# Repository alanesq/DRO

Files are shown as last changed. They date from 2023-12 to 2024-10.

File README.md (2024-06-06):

# DRO - A super cheap Digital Readout (DRO) for lathes, milling machines etc. 

<br>My homemade ESP32 based DRO which conists of:
 - [Cheap Yellow Display](https://github.com/witnessmenow/ESP32-Cheap-Yellow-Display) &ensp; (A.K.A. ESP32-2432S028R) which costs around £12 from Aliexpress
 - Digital calipers which cost under £2.50 each on Aliexpress 
 - Plus a few transistors, general wiring etc... 

As a result, building a three-axis DRO for your milling machine or lathe can set you back less than £25 (around $30). <br><br>

<p align="center" width="100%">
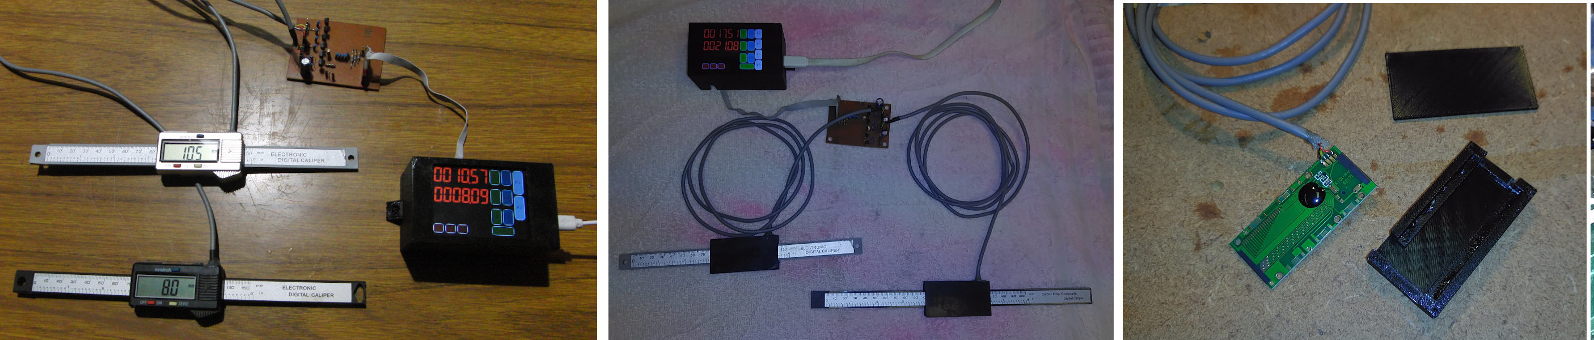
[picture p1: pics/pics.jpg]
  <br><br>
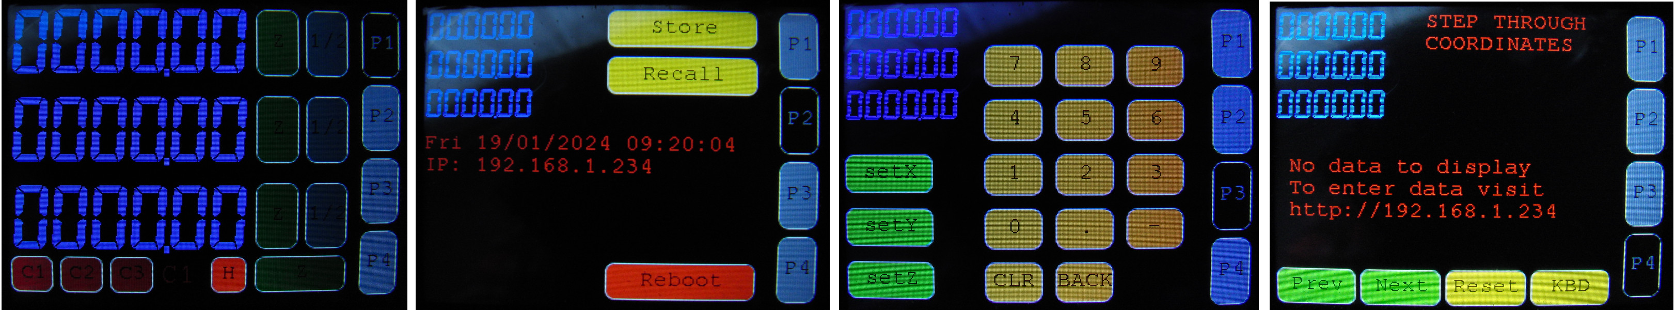
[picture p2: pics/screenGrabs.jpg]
  
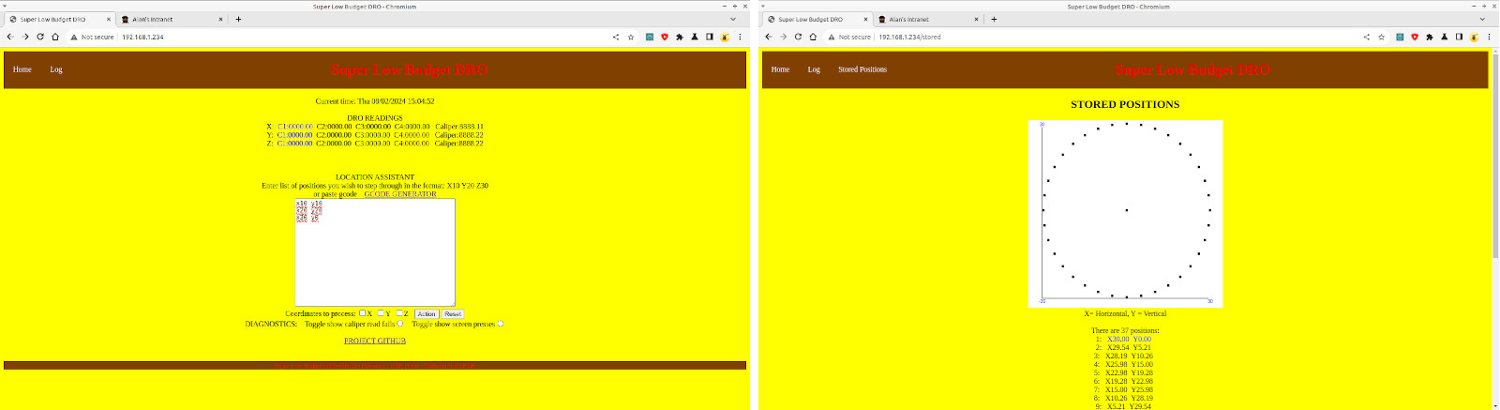
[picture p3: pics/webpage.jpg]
  <br><br>
</p>

I wanted a Digital Readout (DRO) for both my lathe and milling machine. However, the cheapest options available was still going to cost me several hundred pounds, which I just couldn’t justify spending. I also suspected that the cheapest DRO on the market would probably fail after a short time anyway going on my past experience of cheap electronics.  Therefore, I decided to see if I can create my own as inexpensively as possible.  I think it safe to say that I have achieved this goal :-)<br>
Not only did this save me spending a lot of money when I do not even know how much I would use one but it means I can modify it to my exact requirements and it will always be easily fixable.<br><br>

The libraries required for this sketch are detailed [HERE](https://github.com/alanesq/DRO/tree/main/LIBRARIES)<br>
Note that the "TFT_eSPI" library needs to be modified to work with the CYD and if your CYD has two USB ports there is a further change to this required.

## Patterns

Rather than a complicated hole pattern facilities on this DRO (for drilling a circle of holes etc.) I decided it would be easier and more versatile to enter the coordinates of the positions required via the web page, these coordinates can then be steped through from the DRO screen (page 4).  <br>
The coordinates are ented as a simple list in the format:<br>
```
x0 y0
x0 y10
x10 y0
x10 y10
```
It also has the option to paste simple gcode, this gives the ability to create your own bolt hole patterns etc. using whatever software you preffer (A good choice would be Inkscape and [Krabzcam](https://github.com/mkrabset/krabzcam) ) or even easier you can use online tools for creating them &ensp; e.g. [online gcode tools](https://www.intuwiz.com/drilling.html) <br><br>

## Digital calipers

The cheap calipers only have a range of 150mm although longer 200mm or even 300mm are available on eBay for under £20, this is probably enough for my requirements although I have had some longer PCBs created which were designed by "Limi DIY" and they appear to work and extend the range to around 400mm.  There is the possibility to link these together although the join would need to be very accurate.  I had 5 lengths made which came in at £10 each so they are not cheap by the standards of this project but not as expensive as you may think. <br> 
&ensp; &ensp; [extending the range](https://hackaday.com/2021/08/05/custom-caliper-tracks-for-when-youre-going-the-distance/) &ensp; - &ensp;
[PCBway order link](https://www.pcbway.com/project/shareproject/Digital_Caliper_Hack_Mod_new_2021.html) <br>

Especially on my lathe I found that I actually did not need to have a long caliper as the work I require to measure tends to be in a small area so I have just attached a short caliper body to the machine but the slider is attached via a magnet, so if I extend beyond the calipers reach it simply detatches and then re-attaches when it returns.  This works really well and made installing the DRO very simple.  I also have the third caliper on my lathe fully attached with magnets and have two locations I can choose to attach it.  [see pic here](https://github.com/alanesq/DRO/blob/main/pics/lathe1.jpg)<br>

These cheap calipers really are amazing for the price, in fact they are so cheap that it feels like they are almost being given away, also, I find the cheaper ones with a plastic slider are better than metal ones in this application as you do not get issues with the metal contacting the metal of your machine which can cause issues.  Big Clive has made a nice video showing what is inside them and how to take them apart etc.: &ensp; [Big Clive](https://www.youtube.com/watch?v=fKSSY1gzCEs) <br>
I have read that because of interference issues this type caliper is not at all suitable to use as a DRO and I was starting to agree as I had a lot of trouble at first with this but I eventually found the solution (see bottom of page for more info.).<br>
One good thing that I was not expecting is you still get two decimal places from these very cheap calipers even though they only display one on their LCD, as can be seen in the pictures above. <br>

The most recent calipers i have purchased were:   [eBay £5.40 each](https://www.ebay.co.uk/sch/i.html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) , [Aliexpress £10 for 4](https://www.aliexpress.com/item/1005005699974701.html) <br><br>   

## Warnings!

The well known problem with these cheap calipers is the battery goes flat if you do not use them for a while, it turns out that they are producing the data we use here all the time, even when turned off.  I bought one of the longer calipers recently which looks like it is a "new/impoved" design which has got round this issue by turning off the data all together which is very bad news if you want to use it for this project.  So if you are buying calipers I suggest you try to buy the older style ones if you can as the newer ones do not seem to support data, the good news is these will be the cheapest ones.  You can still use the reader from a cheaper caliper on this longer bar if you do have one though.  I understand that some of these calipers use a different data standard although all the ones I have tried are the same.  The calipers would not cope well to getting wet so you will need to cover them well if this is likely to happen.

## Misc info:

I have recently given one of my DROs to the most excellent Youtuber Steamhead - You can see it [HERE](https://youtu.be/Z2Sz5ipYt7Y?si=eyIY_YAoHz-dP2uL&t=618)<br>

Brian Lough's information on the [Cheap Yellow Display](https://github.com/witnessmenow/ESP32-Cheap-Yellow-Display)
  
Communicating with the digital calipers
- [Martin's Creations](https://sites.google.com/site/marthalprojects/home/arduino/arduino-reads-digital-caliper)
- [Robot Room](https://www.robotroom.com/Caliper-Digital-Data-Port.html) - includes some info on different data protocols 
- [electronoobs](http://electronoobs.com/eng_arduino_tut93.php)
- [wei48221](http://wei48221.blogspot.com/2016/01/using-digital-caliper-for-digital-read_21.html)

This sketch is wifi enabled, this is turned off by default but can be turned on via the DROs menu (You can enable wifi at startup by changing a flag in settings.h).  It is useful for OTA updates and for entering drill hole patterns etc.  BTW - I have been very surprised at the range I get from it's wifi.<br>
At present the display has zero buttons for each axis along with a divide by zero button plus buttons to switch to different display pages.  There is plenty of scope to add lots of other features later, I have an idea that it may be nice to have the option to enter a list of points via the web page then have the DRO guide me to each point? <br>
On page 3 of the display there is a number entry keypad which at present is only used to enter a number to jump to on page 4 (by pressing KBD) but it has the potential for other uses, it stores the entered number in to a float and a String.<br>
Note: The first time you start wifi it will create a wifi hotspot which you can connect to in order to enter your local wifi login details.

If you have a 3D printer this is a case I have modified to be large enough to contain all the electronics: &ensp; [custom case](https://github.com/alanesq/DRO/tree/main/case) <br>
Also a replacement case for the digital calipers: &ensp; [caliper case](https://github.com/alanesq/DRO/tree/main/caliperCase)

Current Wifi Features:
- Simulate pressing the screen with: http://x.x.x.x/touch?x=100&y=50
- Restart esp32 with: http://x.x.x.x/reboot
- Check it is live with: http://x.x.x.x/ping
- Log of activity: http://x.x.x.x/log
- Testing code: see 'handleTest' at bottom of page, access with http://x.x.x.x/test
- Update via OTA: http://x.x.x.x/ota

If just connecting one caliper you could use (GPIO 22 and 27) via the CYD connectors but to find enough GPIO pins to read 3 calipers I had to get a bit more creative; I removed the onboard 3 colour LED and then soldered some ribbon wire directly on to one side of the ESP32 module it's self.  This is not as difficult as you might imagine, if you use a small soldering iron tip and magnification it was pretty easy even with my uncoordinated soldering skills.  Tin the pins first ideally using some extra flux, then attach the wires and use some hot melt glue to hold the ribbon wire in place.  I soldered 8 wires to the ESP module plus two to a nearby connector for the 3.3v power.
 - [GPIO pins available to use](https://github.com/alanesq/DRO/blob/main/pics/CYD-gpioPins.jpg)
 - [GPIO pins I used](https://github.com/alanesq/DRO/blob/main/PCB/ribbonCablePins.jpeg) <br>

The wiring is not as complex as it might look, it is just a simple transistor on each data pin to convert from 1.5v up to 3.3v for the esp32 to be able to read, I use my CNC router to create the circuit boards but this could be easily built on some strip board etc.  I tried using a level shifter board at first but I don't think it worked very well with the 1.5v levels. <br>
Note: the transistors to convert the 1.5v signals from the caliper results in the signal levels being inverted so if you use some other method you will need to change 'invertCaliperDataSignals' to 0.  The circuit diagram I used can be seen in the PCB folder along with the files I used to create the circuit boards (Fritzing and CNC router).  To supply the lower voltage to power the caliper I just use a simple voltage divider although after reading in several places what a bad idea this was I tried using a string of diodes instead but this caused the calipers to become very unstable so I converted back.<br>
The best way I found to wire the calipers is to use shielded cable.  I connect the shield and negative power together at the interface end of the wire then at the caliper end I do not connect the sheild to anything and connect the negative wire to the metal of the lathe/mill (i.e. mains earth).  When connected this way I find the displays very stable, only fluctuating by 100th mm at most.<br>

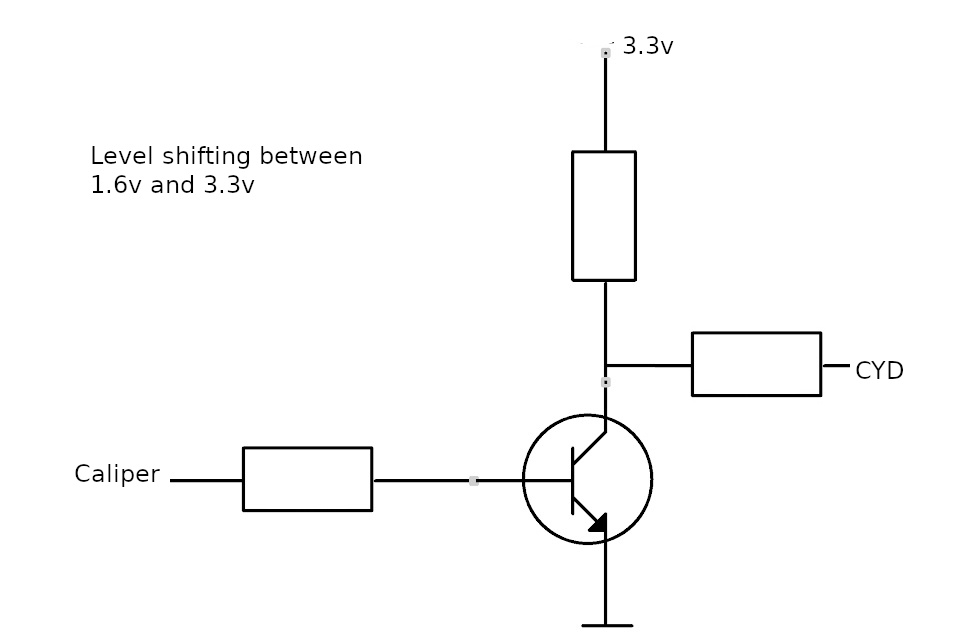
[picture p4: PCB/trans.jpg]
<br>
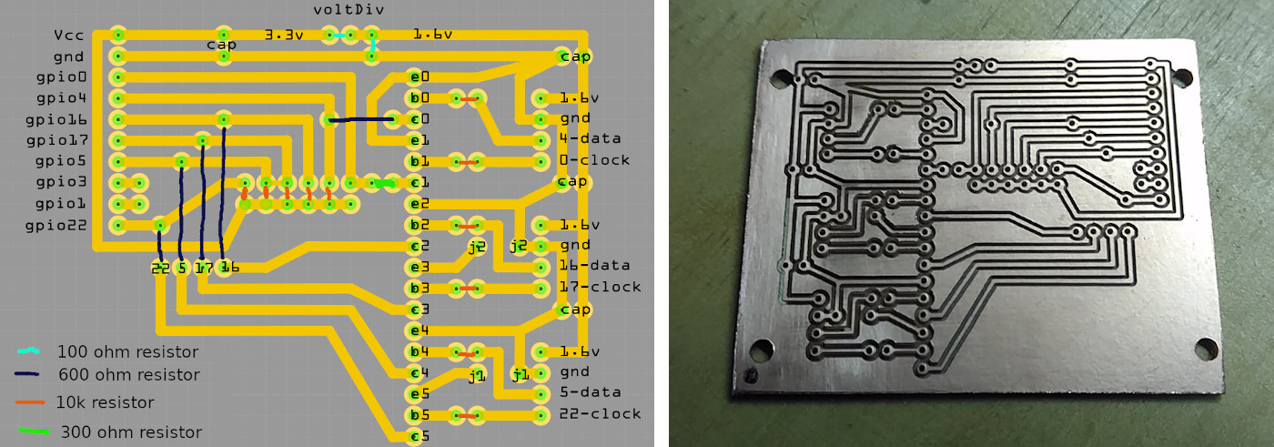
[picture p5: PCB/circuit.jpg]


Note: I am using GPIO0 which isn't ideal as it is also attached to the onboard button, but if you do not install the pull-up resistor and use a lower value resistor on the input this seems to work fine (although it can stop the hardware reset working when programming the CYD).

There are connections for GPIO1 and 3 which are the serial pins but could possibly be used as general GPIO if required? (it can be programmed by OTA so this would not be a big problem).

In an attempt to try and make the calipers more robust I have put some insulation tape over the circuit board (where the slider runs along it) as I think the bare circuit board is very vulnerable to damp entering and corroding the board. &ensp; [Picture](https://github.com/alanesq/DRO/blob/main/pics/caliperMod.jpg) <br>
It may also be an idea to coat the rest of the circuit board in some kind of conformal coating (clear nail varnish?) and maybe some kind of dust seal around the slider where it enters the reader (I believe some come with one fitted).
<br>One advantage of having the remote display is it will make it easier to fit the calipers out of harms way as you do not need to see the display on them.

At present it is set up to have 4 display pages, buttons can be created and assigned to the pages in the "define the button widgets" section of the sketch.  The caliper readings are displayed on all pages but there are two sizes available (this size is set in "displayReadings").  Button actions are defined in the "buttons.h" file.  It has a demo keypad for entering numbers but it is not yet used for anything.  I plan to add more features later on.  Let me know if there are features you would like me to add? <br><br>

On page 2 there is the option to store the current readings and recall them.  This is stored in eeprom so can be recalled even after the device has been turned off.  <br>
On page 1 there is a hold button "H" which I created when I was having trouble with interference causing the displays to jump about, this reads the current values, waits a while then restores them, I have left it as it may prove of some use one day?

On my lathe I have a stop which I can attach to make sure I don't take the carriage too far, as a temp. test I attached a caliper to this but it actually worked out so well I have kept it this way.  The end of the calipers slider attaches with a strong magnet so if I take the carriage too far it just detaches and re-attaches when it returns. [picture](/pics/lathe1.jpg) <br>

## Troubleshooting

Not enough memory when compiling:  If using the latest esp32 board drivers it seems to require a lot more memory than the older ones, if you set the partition scheme to "Minimal spiffs" this should resolve the issue.

If you find the caliper readings are unstable, jump about (often in 5mm steps) I have found that the power supply is important for the calipers in that most switch mode USB power supplies seem to cause them to give random readings which jump about and are completely unstable.  I also had a lot of trouble with switching the lathe on/off would cause the caliper readings to jump.  A linear power supply is probably a good idea but I used a PC power supply for mine in the end although I have since discovered that connecting the negative power feed to the calipers to mains earth  i.e. the metal of the mill/lathe (near to the caliper if possible) is by far the most important thing, this makes a massive difference.  Also a big capacitor on the power feed to the calipers helps a lot (I used a 3000uF).  I had considered using a linear regulator to power the CYD from the 5v USB to cut out the switched mode power supply noise but the CYD has two 3.3v regulators onboard so i don't think you can easily power it from 3.3v

I sometimes find that if the DRO has not been used for a while the calipers don't seem to power up in the correct state which can result in one or more of them not responding, if you turn the DRO off for a few seconds and back on this usually resolves the issue.  I guess they are not designed to have the battery removed, this could be resolved by giving the DRO control of the power to the calipers so it can power cycle them at startup, in fact they draw so little power that a gpio pin could probably power them directly (via voltage divider).  Another option which may be worth considering is just power the calipers from a AA battery and leave them powered all the time, they are designed to run from a watch battery so it should last a reasonable time and this would also avoid any issues with power supplies.

If you enable showing of caliper read errors this can help decide if there is a problem with one of the calipers.  I find that if running it from a standard USB power supply you can get a lot of read errors although it stilll functions ok, on mine which are running from an old PC power supply I get pretty much no read errors at all.

If the screen colours seem very odd or if you find the CYD reboots as soon as a button is pressed this is probably becuase the User_Setup.h file has not been copied over for the "TFT_eSPI" library [see here](https://github.com/witnessmenow/ESP32-Cheap-Yellow-Display/blob/main/SETUP.md)
Note: I have had issues where I change something in the library settings and even when I change it back it no longer works.  This is becuase the Arduino IDE doesn't re-compile everything, every time so to get it to re-compile I close the Arduino IDE and re-open it after the change.

One possible issue I anticipate is that the calipers often have a random reading when first powered on, this could be a problem if it is close to the limit of the caliper if you then move it past this limit (the limit looks to be 9999.99mm on mine?).  It can of course be solved simply by pressing the zero button on the caliper but this is something I may look in to later.  I believe the caliper can be zeroed by taking one of the data pins to ground but this would require extra circuitry.

I have had a lot of issues with interference from the motor switching on/off on my lathe and to lesser extent my mill. This interference usually seems to cause the caliper to jump up or down in 5mm steps, this it turns out is a common issue when using this type caliper. 
I tried all sorts of things to try and improve this but after a lot of experimentation and head scratching I finally discovered that in my case at least the solution was to use shielded cable from the esp32 interface to the calipers with the shield connected to the GND (Esp32 end).  At the caliper end I connect the shield to the metal of the lathe/mill (i.e. mains earth).  I do not know if this is a "good idea" electronics wise but the result is almost spectacular with a rock solid reading even when turning the motor on and off repeatedly :-)

--------------------------------------

## Contact

If you use this sketch please let me know how you get on and if you have any suggestions for improvments etc.  - alanesq@disroot.org

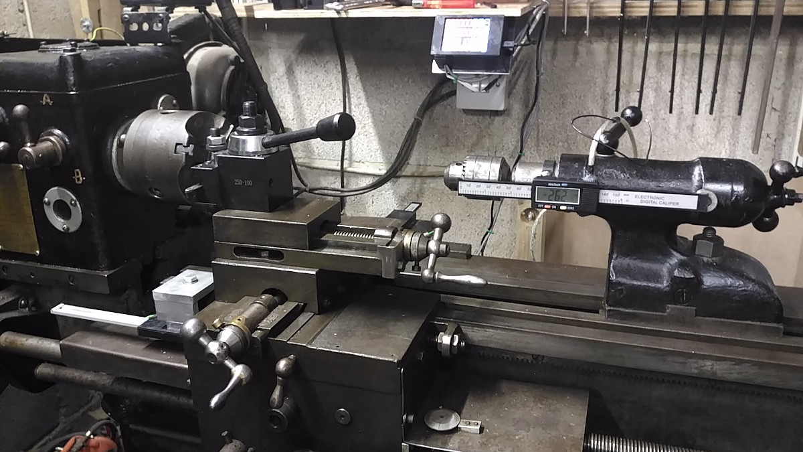
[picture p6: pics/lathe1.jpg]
<br><br>

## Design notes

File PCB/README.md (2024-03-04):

#PCB to interface the CYD to the digital calipers

 <br>


The calipers operate at 1.5v so this is required to convert this to the 3.3v of the CYD.  It is a very simple circuit which uses a single transistor per data pin, I used my CNC router to cut a PCB but you could easily just build this on some strip board etc. I have seen others use the level shifters from eBay but I could not get mine to operate with the 1.5volts. <br>
I think if I were building another one I would seriously consider using a AA battery to provide the 1.5v for the calipers rather than using the 5v power rail, this would get round a lot of potential issues with noise on the power line upsetting the calipers and issues of them not starting up correctly when the power is first applied.<br>

The calipers are linked to the CYD via a ribon cable soldered directly to the ESP32 module (the 3 colour led needs to be removed).<br>
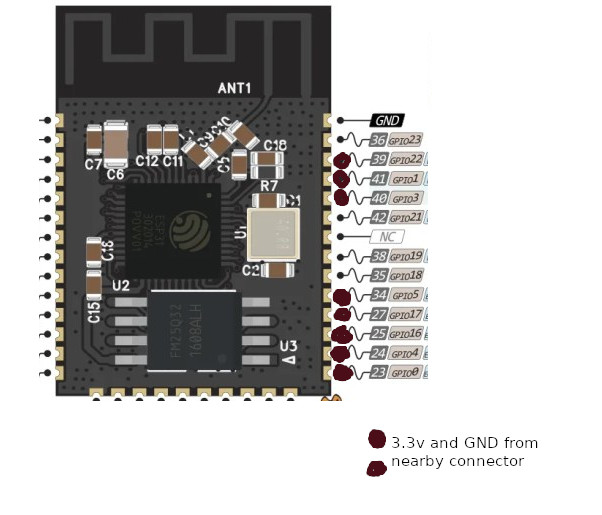
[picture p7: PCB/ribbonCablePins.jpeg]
 <br>

See [the main page](https://github.com/alanesq/DRO) for more info. <br>

--------------------
https://github.com/alanesq/DRO - alanesq@disroot.org

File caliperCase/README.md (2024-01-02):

#3D printable case for digital caliper reader

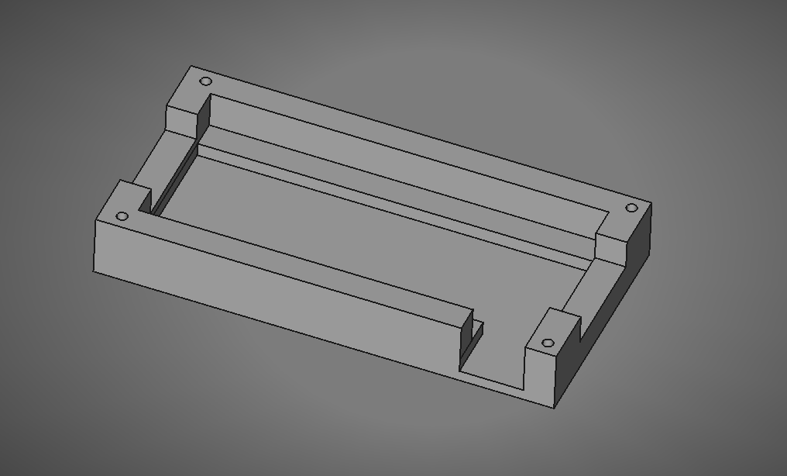
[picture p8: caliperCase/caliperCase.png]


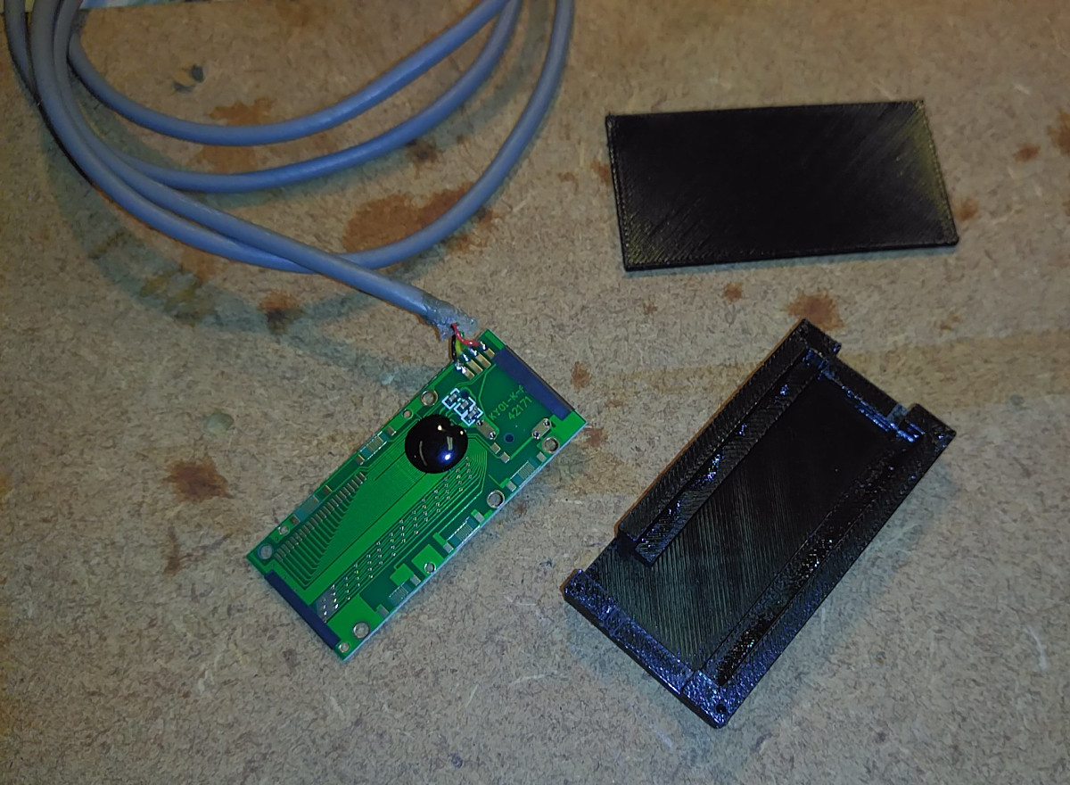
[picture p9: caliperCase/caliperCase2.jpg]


This is a case I created for the digital calipers reader circuit board
The battery holder has to be removed from the PCB (they often just pull off as they are not soldered) and it can be installed in this case without the LCD display.

I have included the Freecad file and STL files

--------------------
https://github.com/alanesq/DRO - alanesq@disroot.org

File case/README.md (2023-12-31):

#3D printable case for the DRO project

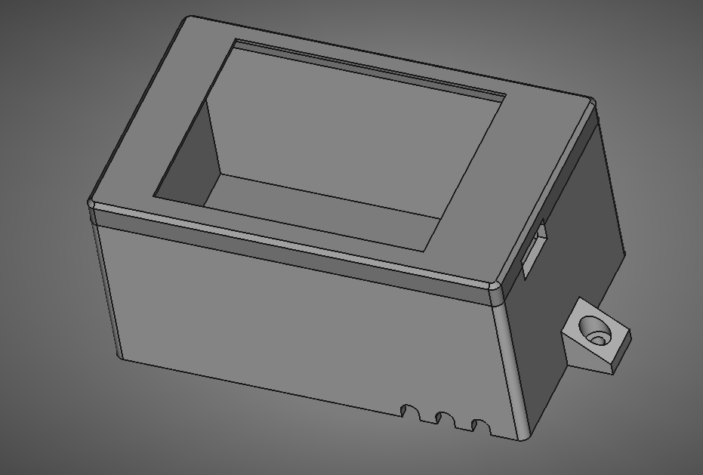
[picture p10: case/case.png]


The idea behind this case is the interface circuit board is attached to a surface (via pillars)
and then this case screws on to the base over the top of this circuit board
This way the case can be removed easily leaving the interface and all its cables in place.

The case can print with no supports if printed top side down
It takes around 2hrs on my printer

I have included an STL file for it along with the Freecad file

[The case here is based on this one created by mdkendall](https://www.printables.com/model/685845-enclosure-for-sunton-esp32-2432s028r-cheap-yellow-)

--------------------
https://github.com/alanesq/DRO - alanesq@disroot.org

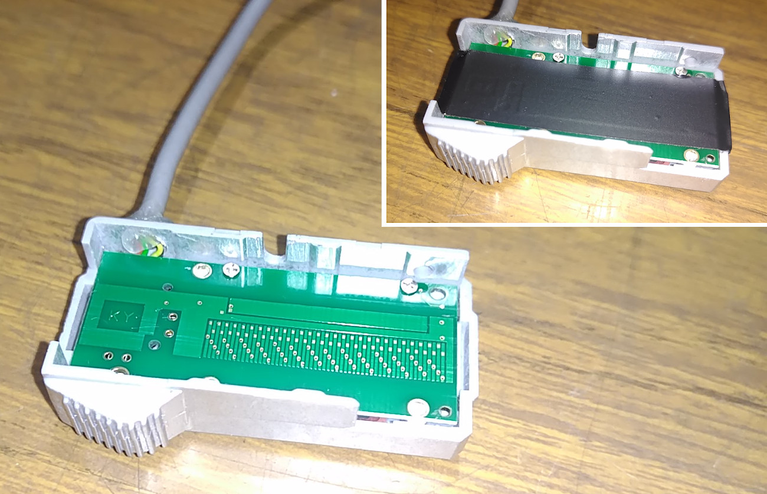
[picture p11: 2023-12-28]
pics/caliperMod.jpg

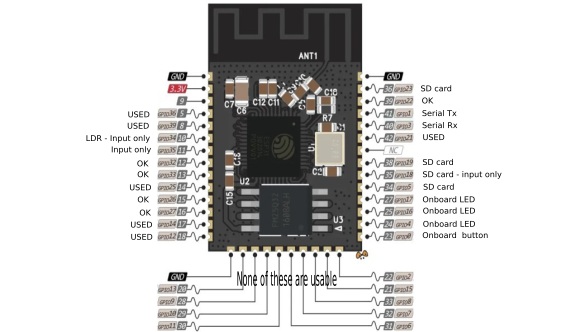
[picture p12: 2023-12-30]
pics/CYD-gpioPins.jpg

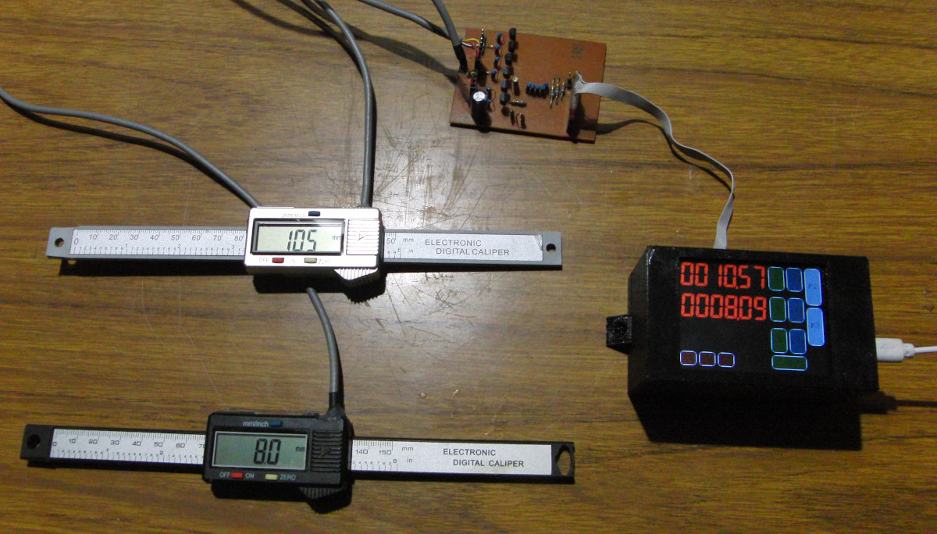
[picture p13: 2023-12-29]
pics/DROproject.jpg

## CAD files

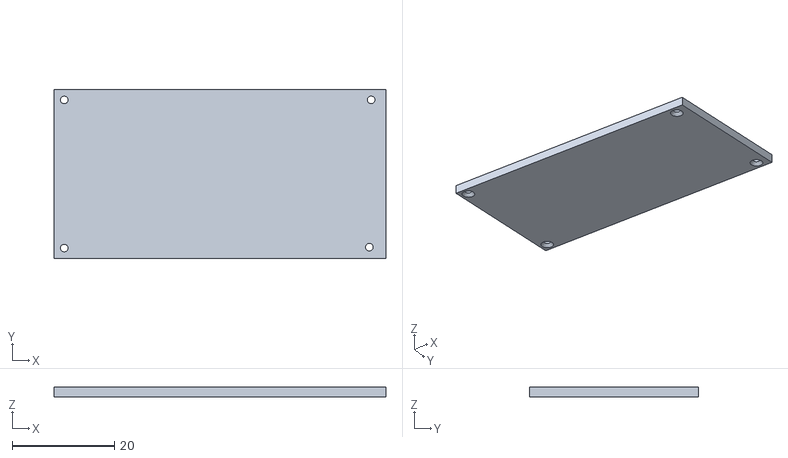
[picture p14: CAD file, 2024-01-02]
caliperCase/caliperCaseLid.stl
65.0 x 33.0 x 2.00

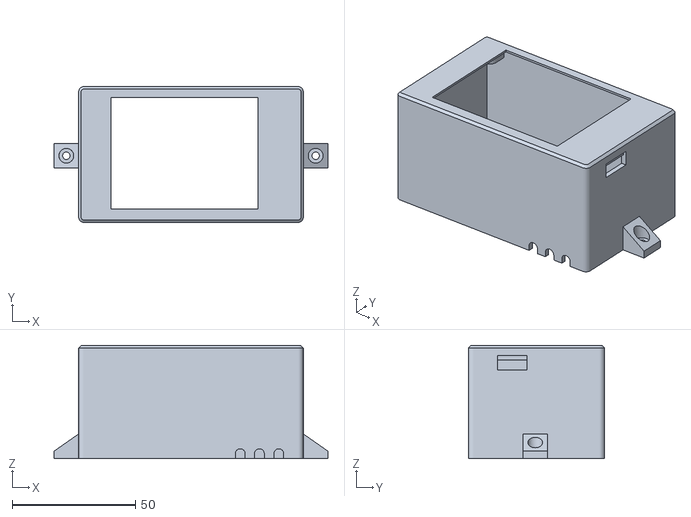
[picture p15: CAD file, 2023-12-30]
case/case.stl
111.0 x 55.0 x 45.9

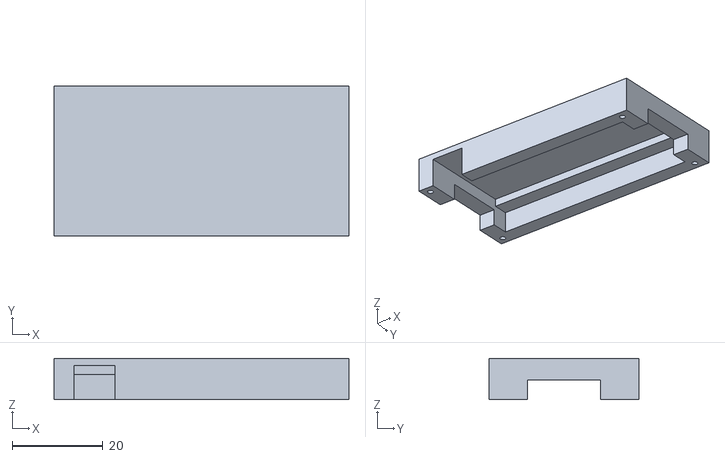
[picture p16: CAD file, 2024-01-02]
caliperCase/caliperCase.stl
65.0 x 33.0 x 9.10

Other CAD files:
case/case-freecad.FCStd
caliperCase/caliperCasingv.FCStd

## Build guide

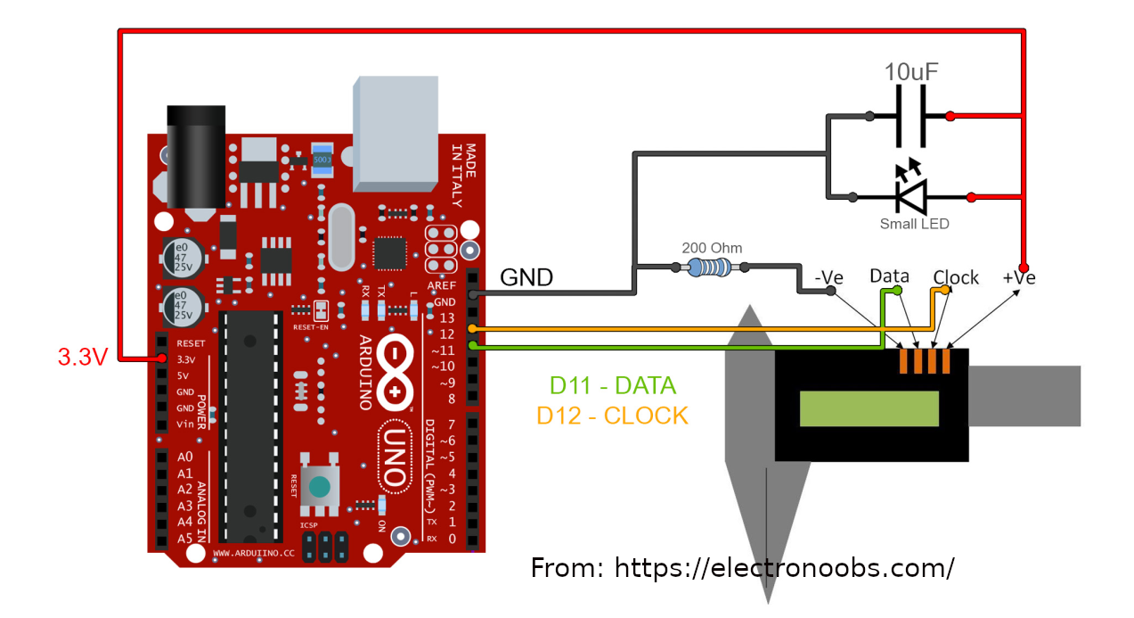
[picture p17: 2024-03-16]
pics/wiring.png

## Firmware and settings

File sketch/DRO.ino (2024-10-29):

/*******************************************************************************************************************
 *
 *                                              SuperLowBudget-DRO               29Oct24
 *                                              ------------------
 *
 *          3 Channel DRO using cheap digital calipers and a ESP32-2432S028R (aka Cheap Yellow Display)
 *                     see: https://github.com/witnessmenow/ESP32-Cheap-Yellow-Display
 *
 *                                      https://github.com/alanesq/DRO
 *
 *
 *                         Tested in Arduino IDE 2.3.0 with Espressif board manager ESP32 2.0.14
 *
 *                 Included files: settings.h, standard.h, ota.h, sevenSeg.h, Free_Fonts.h, buttons.h & wifi_dro.h
 *
 *   If using WifiManager the first time the ESP starts it will create an access point "ESPDRO" which you need to connect to 
 *    in order to enter your wifi details.  Default password = "password"   (change this in wifi_dro.h)
 *    for more info. see: https://www.youtube.com/watch?v=Errh7LEEug0
 *
 *
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
 ********************************************************************************************************************

  Libraries used:     https://github.com/PaulStoffregen/XPT2046_Touchscreen - 1.4
                      https://github.com/Bodmer/TFT_eSPI - 2.5.34
                      https://github.com/Bodmer/TFT_eWidget - 0.0.5
                      https://github.com/tzapu/WiFiManager - 2.0.16         


  Ribbon cable soldered to one side of the esp32 module: https://github.com/alanesq/DRO/blob/main/PCB/ribbonCablePins.jpeg
  The 3 colour LED should be removed.
    3.3v      (from nearby connector)
    gnd       (from nearby connector)
    gpio 0    Caliper X clock
    gpio 4    Caliper X data
    gpio 16   Caliper Z clock
    gpio 17   Caliper Y clock
    gpio 5    Caliper Y data
    gpio 3    Serial Rx    
    gpio 1    Serial Tx 
    gpio 22   Caliper Z data

  Pins that should be ok to use: 22, 32, 33, 26 (also 35, 18 which are input only)
  other possible use pins: 4, 16, 17 (onboard LED) : 5, 23, 18, 19 (sd card) : 1, 3 (Serial) 0 (onboard button) : 34 (LDR)


  Test Points:
      S1	GND	              near USB-SERIAL
      S2	3.3v	              for ESP32
      S3	5v	              near USB-SERIAL
      S4	GND	              for ESP32
      S5	3.3v	              for TFT
      JP0 (pad nearest USB socket)    5v TFT LDO
      JP0	3.3v	              TFT LDO
      JP3 (pad nearest USB socket)    5v ESP32 LDO
      JP3	3.3v	              ESP32 LDO    


    Digital Caliper pinout (VCC = edge of circuit board): 
          VCC (1.5V) - I just use a simple voltage divider of 100ohm resistors to supply 1.65v as they use very little power
          CLOCK
          DATA
          GND


    Colours available to use on display: 
          TFT_BLACK, TFT_NAVY, TFT_DARKGREEN, TFT_DARKCYAN, TFT_MAROON, TFT_PURPLE, TFT_OLIVE,
          TFT_LIGHTGREY, TFT_DARKGREY, TFT_BLACK, TFT_GREEN, TFT_CYAN, TFT_RED, TFT_MAGENTATFT_YELLOW,
          TFT_WHITE, TFT_ORANGE, TFT_GREENYELLOW, TFT_PINK, TFT_BROWN, TFT_GOLD, TFT_SILVER, TFT_SKYBLUE, TFT_VIOLET


    Wifi features:
      Simulate pressing the screen:       http://x.x.x.x/touch?x=100&y=50
      Restart the esp32:                  http://x.x.x.x/reboot
      Check if it is live:                http://x.x.x.x/ping
      Log of activity:                    http://x.x.x.x/log
      Testing code:                       http://x.x.x.x/test               (see 'handleTest()' at bottom of page)
      Update via OTA:                     http://x.x.x.x/ota                (default password is 'password')
      List stored positions               http://x.x.x.x/stored

*/

#if (!defined ESP32)
  #error This code is for the ESP32 based 'Cheap Yellow Display' only
#endif

#include <Arduino.h>                      // required to use Strings 
String enteredGcode;                      // store for the entered gcode on web page
#include "settings.h"                     // load in settings for the DRO from settings.h file

#include <esp_task_wdt.h>                 // watchdog timer   - see: https://iotassistant.io/esp32/enable-hardware-watchdog-timer-esp32-arduino-ide/     

// wifi
  void log_system_message(String smes);   // in standard.h
  int wifiok = 0;                         // flag if wifi connection is ok 
  #include <wifi_dro.h>

// forward declarations
  //void log_system_message(String smes);   // in standard.h
  void handleRoot();
  void handleData();
  void handlePing();
  void settingsEeprom(bool eDirection);
  void handleTest();
  void drawScreen(int);      
  void displayReadings(bool clearFirst = 0);
  void startTheWifi();
  bool refreshCalipers(int cRetry, bool display = 1); 
  void clearGcode();
  void plotGraph(WiFiClient &client, int axis1, int axis2);
  float mapf(float x, float in_min, float in_max, float out_min, float out_max);
  void loadTestPositions();
  


  // -------------------------------------------- CYD DISPLAY --------------------------------------------

    #include <SPI.h>
    #include <FS.h>
    #include <XPT2046_Touchscreen.h>

    SPIClass mySpi = SPIClass(HSPI);            // note: I had to change VSPI to HSPI
    XPT2046_Touchscreen ts(XPT2046_CS, XPT2046_IRQ);  

    #include <TFT_eSPI.h>                       // display driver
    #include <TFT_eWidget.h>                    // Widget library
    #include "Free_Fonts.h"                     // Standard fonts info
    #include "sevenSeg.h"                       // seven segment style font
    TFT_eSPI tft = TFT_eSPI();
      
    MeterWidget dro  = MeterWidget(&tft);       // Meter used at startup

    unsigned long lastTouch = 0;                // last time touchscreen button was pressed
    
    // entered gcode
      float gcode[caliperCount][maxGcodeStringLines];    // store for positions extracted from the gcode
      int gcodeLineCount = 0;                   // number of positions that have been extracted from the gcode
      bool inc[caliperCount] = {0};             // which coordinates to process
      int gcodeStepPosition = 1;                // current position in the extracted positions
      float gcodeDROadj[caliperCount] = {0};    // temp adjustments to DRO readings for locating position when stepping through gcode positions


// --------------------------------------- Menu / buttons ---------------------------------------

  // font to use for all buttons  
    #define MENU_FONT FM9                                // standard Free Mono font - available sizes: 9, 12, 18 or 24
    #define MENU_SIZE 2                                  // font size (1 or 2)

    // Page selection buttons
    // Note: to add more pages, in 'DRO.ino' increase 'numberOfPages', modify the two sections marked with '#noPages' and add procedures to 'buttons.h'
      const int numberOfPages = 4;                       // the number of pages available (note - it is already configured for 5)
      const int pageButtonWidth = 34;                    // width of the buttons
      const int pageButtonSpacing = 5;                   // space between buttons
      const int pageButtonHeight = (SCREEN_HEIGHT / numberOfPages) - pageButtonSpacing;  // height of each button
  
    // DRO readings size/position settings 
        const int DROdisplaySpacing = 10;                // space between the DRO readings
        const int DROnoOfDigits1 = 4;                    // number of digits to display in caliper readings (before decimal)
        const int DROnoOfDigits2 = 2;                    // number of digits to display in caliper readings (after decimal)
        const int DROwidth = 200;                        // width of DRO reading display   i.e. x position of zero buttons  
        const int DROheight = 200;                       // Height of the DRO reading display for placement of lower buttons  
        const int DRObuttonheight = 30;                  // buttons around DRO readings              
        const int DRObuttonWidth = 35;                     
        const int DROdbuttonPlacement = 70;              // vertical spacing of the DRO buttons  
        
    // page 2 - misc 
      const int p2secondColumn = 150;                    // y position of second column of buttons 
      const int p2buttonSpacing = 8;                     // space between rows of buttons

    // page 3 - numeric keypad 
      const int noDigitsOnNumEntry = 10;                 // maximum length of entered number
      const int keyWidth = 45;
      const int keyHeight = 32;
      const int keySpacing = 10;
      const int keyX = 110;                              // position on screen (top left)
      const int keyY = 30;
      const int setKeyWidth = 65;                        // width os set buttons
      
    // page 4 - gcode
      const int p4ButtonSpacing = 70;                    // button spacing
      const int p4ButtonGap = 4;                         // gap between buttons

    
    int displayingPage = 1;           // which screen page is live

    typedef void (*buttonActionCallback)(void);   // create a function pointer
    
    // struct to create a button
    struct buttonStruct {
      int page;                       // which screen page it belongs to (0 = show on all pages)
      bool enabled;                   // if this button is enabled
      String label;                   // buttons title
      int16_t x, y;                   // location on screen (top left)
      uint16_t width, height;
      uint16_t outlineColour;
      uint16_t outlineThickness;
      uint16_t fillColour;
      uint16_t textColour;
      ButtonWidget* btn;               // button object (widget)
      buttonActionCallback action;     // procedure called when button pressed
    };


  // // create button widgets - better technique but I think this would need to be in setup?
  //   const int numberOfWidgets = 45;    // the number of buttons required
  //   ButtonWidget butnW[numberOfWidgets] = {nullptr};
  //   for (int i = 0; i < numberOfWidgets; ++i) {
  //     buttonWidgets[i] = new ButtonWidget(&tft);
  //   }    

  // create the button widgets - there has to be a better way? - ensure there are enough for the number of buttons required (check log to verify)
    ButtonWidget butnW[] = { &tft, &tft, &tft, &tft, &tft, &tft, &tft, &tft, &tft, &tft, &tft, &tft, &tft, &tft, &tft, &tft, &tft, &tft, 
                             &tft, &tft, &tft, &tft, &tft, &tft, &tft, &tft, &tft, &tft, &tft, &tft, &tft, &tft, &tft, &tft, &tft, &tft, 
                             &tft, &tft, &tft, &tft, &tft, &tft, &tft, &tft, &tft };   
    int widgetCount = (sizeof(butnW) / sizeof(*butnW)) - 1;     // counter used for assigning widgets to buttons


  // keypad (Page 3)
    String keyEnteredNumber = "";      // the number entered on the keypad (String)
    float keyEnteredNumberVal = 0;     // the above string as an float


  // ---------------------------------- -define the button widgets --------------------------------------

    #include "buttons.h"             // the procedures which are triggered when a button is pressed

    const int buttonSpacing = 6;     // spacing used when placing the buttons on display
  
    buttonStruct screenButtons[] {               

    // all pages
      // page selection buttons - #noPages
      //    page, enabled, title, x, y, width, height, border colour, burder thickness, fill colour, pressed colour, button, procedure to run when button is pressed
      {0, 1, "P1", SCREEN_WIDTH - pageButtonWidth, (pageButtonHeight + pageButtonSpacing) * 0, pageButtonWidth, pageButtonHeight, TFT_WHITE, 1, TFT_SILVER, TFT_BLACK, &butnW[widgetCount--], &OnePage1Pressed},
      {0, 1, "P2", SCREEN_WIDTH - pageButtonWidth, (pageButtonHeight + pageButtonSpacing) * 1, pageButtonWidth, pageButtonHeight, TFT_WHITE, 1, TFT_SILVER, TFT_BLACK, &butnW[widgetCount--], &OnePage2Pressed},
      {0, 1, "P3", SCREEN_WIDTH - pageButtonWidth, (pageButtonHeight + pageButtonSpacing) * 2, pageButtonWidth, pageButtonHeight, TFT_WHITE, 1, TFT_SILVER, TFT_BLACK, &butnW[widgetCount--], &OnePage3Pressed},
      {0, 1, "P4", SCREEN_WIDTH - pageButtonWidth, (pageButtonHeight + pageButtonSpacing) * 3, pageButtonWidth, pageButtonHeight, TFT_WHITE, 1, TFT_SILVER, TFT_BLACK, &butnW[widgetCount--], &OnePage4Pressed},
      {0, 1, "P5", SCREEN_WIDTH - pageButtonWidth, (pageButtonHeight + pageButtonSpacing) * 4, pageButtonWidth, pageButtonHeight, TFT_WHITE, 1, TFT_SILVER, TFT_BLACK, &butnW[widgetCount--], &OnePage5Pressed},

    // Page 1

      // Zero buttons
      {1, calipers[0].enabled, "Z", DROwidth, 0, DRObuttonWidth, DRObuttonheight * 2 - buttonSpacing, TFT_WHITE, 1, TFT_DARKGREEN, TFT_BLACK, &butnW[widgetCount--], &zeroXpressed},
      {1, calipers[1].enabled, "Z", DROwidth, DROdbuttonPlacement * 1, DRObuttonWidth,  DRObuttonheight * 2 - buttonSpacing, TFT_WHITE, 1, TFT_DARKGREEN, TFT_BLACK, &butnW[widgetCount--], &zeroYpressed},
      {1, calipers[2].enabled, "Z", DROwidth, DROdbuttonPlacement * 2, DRObuttonWidth,  DRObuttonheight * 2 - buttonSpacing, TFT_WHITE, 1, TFT_DARKGREEN, TFT_BLACK, &butnW[widgetCount--], &zeroZpressed},
      {1, 1, "Z", DROwidth, DROheight, DRObuttonWidth * 2 + buttonSpacing,  DRObuttonheight, TFT_WHITE, 1, TFT_DARKGREEN, TFT_BLACK, &butnW[widgetCount--], &zAllpressed},

      // half buttons
      {1, calipers[0].enabled, "1/2", DROwidth + DRObuttonWidth + buttonSpacing, 0, DRObuttonWidth,  DRObuttonheight * 2 - buttonSpacing, TFT_WHITE, 1, TFT_DARKCYAN, TFT_BLACK, &butnW[widgetCount--], &halfXpressed},
      {1, calipers[1].enabled, "1/2", DROwidth + DRObuttonWidth + buttonSpacing, DROdbuttonPlacement * 1, DRObuttonWidth,  DRObuttonheight * 2 - buttonSpacing, TFT_WHITE, 1, TFT_DARKCYAN, TFT_BLACK, &butnW[widgetCount--], &halfYpressed},
      {1, calipers[2].enabled, "1/2", DROwidth + DRObuttonWidth + buttonSpacing, DROdbuttonPlacement * 2, DRObuttonWidth,  DRObuttonheight * 2 - buttonSpacing, TFT_WHITE, 1, TFT_DARKCYAN, TFT_BLACK, &butnW[widgetCount--], &halfZpressed},
      
      // Coordinate select buttons
      {1, 1, "C1", (DRObuttonWidth + buttonSpacing) * 0, DROheight, DRObuttonWidth,  DRObuttonheight, TFT_WHITE, 1, TFT_MAROON, TFT_BLACK, &butnW[widgetCount--], &coord1pressed},
      {1, 1, "C2", (DRObuttonWidth + buttonSpacing) * 1, DROheight, DRObuttonWidth,  DRObuttonheight, TFT_WHITE, 1, TFT_MAROON, TFT_BLACK, &butnW[widgetCount--], &coord2pressed},
      {1, 1, "C3", (DRObuttonWidth + buttonSpacing) * 2, DROheight, DRObuttonWidth,  DRObuttonheight, TFT_WHITE, 1, TFT_MAROON, TFT_BLACK, &butnW[widgetCount--], &coord3pressed},
      {1, 1, "C4", (DRObuttonWidth + buttonSpacing) * 3, DROheight, DRObuttonWidth,  DRObuttonheight, TFT_WHITE, 1, TFT_MAROON, TFT_BLACK, &butnW[widgetCount--], &coord4pressed},
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
void loop() {

  if(wifiEnabled) server.handleClient();                  // service any web page requests

  refreshCalipers(2);                                     // refresh readings from calipers 

  // Touch screen
    bool st = ts.touched();                               // discover if touch screen is pressed
    if (st && !sTouched) {                                // if touchscreen is pressed and is not already flagged as pressed
      actionScreenTouch(ts.getPoint());                   // call procedure for when screen has been pressed
      sTouched = 1;                                       // flag that the screen is curently pressed
    } 
    if (!st && sTouched) {                                // if touchscreen has been released
      actionScreenRelease(ts.getPoint());                 // call procedure for when screen has been released
      sTouched = 0;                                       // clear screen pressed flag
    }

    // housekeeping
      static repeatTimer checkTimer;                      // set up a repeat timer (see standard.h)
      if (checkTimer.check(8000)) {                       // repeat at set interval (ms)
        esp_task_wdt_reset();                             // reset watchdog timer 
        WIFIcheck();                                      // check wifi connection is ok
        timeStatus();                                     // check if NTP time is ok
        time_t t=now();                                   // read current time to ensure NTP auto refresh keeps triggering (otherwise only triggers when time is required causing a delay in response)
      }  
}


// ----------------------------------------------------------------
//                      -refresh calipers
// ----------------------------------------------------------------
// refresh readings from the digital calipers and update display if anything has changed (int = number of times to retry reading caliper)
// returns 1 if data received ok from all calipers.  
// if display set to false the screen is not updated but the reading is stored even if in error state

bool refreshCalipers(int cRetry, bool display) {

  bool refreshDisplayFlag = 0;                                     // display will be refreshed if this flag is set
  int tCount                           ;                           // temp variables
  bool tOK[caliperCount];                                          // flag if data received form caliper ok
  for (int i=0; i < caliperCount; i++) tOK[i] = 0;

  // Digital Calipers
    for (int c=0; c < caliperCount; c++) {
      if (calipers[c].enabled) {                                   // if caliper is active
        tCount = cRetry;                                           // reset try counter 
        while (tCount > 0 && tOK[c] == 0) {
          float tRead = readCaliper(c);                            // read data from caliper 
          if (tRead < lowestAllowedReading || tRead > highestAllowedReading) calipers[c].error = 1;     // verify reading is in valid range
          if (calipers[c].error == 0) {                            // if caliper read data ok 
            tOK[c] = 1;                                            // flag reading received 
            if (tRead != calipers[c].reading  || calipers[c].lastReadTime == 0) {                       // if reading has changed or this is forst reading
              calipers[c].reading = tRead;                         // store result in global variable 
              refreshDisplayFlag = 1;                              // flag DRO display to update
              calipers[c].lastReadTime = millis();                 // log time of last reading received
            }
          } else {
            // read error
              if (serialDebug) Serial.println(calipers[c].title + " Caliper read failed: " + String(tRead));    
              if (showDROerrors) refreshDisplayFlag = 1;           // if show errors set then flag to display the error
          }   
          tCount --;                                               // decrement try counter
          if (tOK[c] == 0) delay(11);                              // delay before retrying
        }  // while
      } else tOK[c] = 1;                                           // caliper is disabled so skip it
    }  

    if (refreshDisplayFlag && display) displayReadings();          // display caliper readings 
    
    bool tOKres = 1;
    for (int c=0; c < caliperCount; c++) if (tOK[c] == 0 && calipers[c].enabled) tOKres = 0;
    return tOKres;
}    


// ----------------------------------------------------------------
//       -root web page requested    i.e. http://x.x.x.x/
// ----------------------------------------------------------------

void handleRoot() {

  WiFiClient client = server.client();             // open link with client
  webheader(client);                               // html page header  (with extra formatting)

// set the web page's title?
//    client.printf("\n<script>document.title = \"%s\";</script>\n", stitle);

  // log page request including clients IP
    IPAddress cip = client.remoteIP();
    String clientIP = decodeIP(cip.toString());   // check for known IP addresses
    log_system_message("Root page requested from: " + clientIP);

  rootUserInput(client);     // Action any user input from this page

  // Build the HTML
    client.printf("<FORM action='%s' method='post'>\n", HomeLink);     // used by the buttons


// ---------------------------------------------------------------------------------------------
//  info which is periodically updated using AJAX - https://www.w3schools.com/xml/ajax_intro.asp

  // insert area which is later populated via vbscript with live data from http://x.x.x.x/data 
    client.println("<br><span id='uline' style='display: inline-block; min-height: 110px;'></span><br>");


  // Javascript - to periodically update the above info lines from http://x.x.x.x/data
    // get from http://x.x.x.x/data and populate the blank lines in html above

  // this is the below section compacted via https://www.textfixer.com/html/compress-html-compression.php
    client.printf(R"=====( <script> function getData() { var xhttp = new XMLHttpRequest(); xhttp.onreadystatechange = function() { if (this.readyState == 4 && this.status == 200) { document.getElementById('uline').innerHTML = this.responseText; } }; xhttp.open('GET', 'data', true); xhttp.send();} getData(); setInterval(function() { getData(); }, %d); </script> )=====", dataRefresh * 1000);

/*
    client.printf(R"=====(
      <script>
          function getData() {
            var xhttp = new XMLHttpRequest();
            xhttp.onreadystatechange = function() {
            if (this.readyState == 4 && this.status == 200) {
              document.getElementById('uline').innerHTML = this.responseText;
            }
          };
          xhttp.open('GET', 'data', true);
          xhttp.send();}
          getData();
          setInterval(function() { getData(); }, %d);
      </script>
    )=====", dataRefresh * 1000);
*/
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

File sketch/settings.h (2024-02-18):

/* -----------------------------------------------------------------------------------------


          DRO Settings 

          Part of the  "SuperLowBudget-DRO" sketch - https://github.com/alanesq/DRO

          Ensure you have modified the library for working with the CDY - see: https://github.com/alanesq/DRO/tree/main/LIBRARIES
          If using the two usb port version of the 'Cheap Yellow Display' change 'User_Setup_Select.h' in the TFT_eSPI library


// -----------------------------------------------------------------------------------------
*/


                const char* stitle = "Super Low Budget DRO";    

      
                const char* sversion = "18Feb24";              



// ----------------------------------------------------------------------

      
  bool wifiEnabled = 0;                                 // If wifi is enabled by default (can be enabled in DRO menu)
  int wifiType = 1;                                     // Type of wifi to use (1=WifiManager, 2=manual wifi credentials, 3=access point)      

  const String OTAPassword = "password";                // Password to enable OTA (supplied as - http://<ip address>?pwd=xxxx )

  const bool serialDebug = 0;                            // provide debug info on serial port  (disable if using Tx or Rx gpio pins for caliper)
  const int serialSpeed = 115200;                        // Serial data speed to use  

  const bool invertCaliperDataSignals = 1;               // If using transistors on the data and clock pins the signals will be inverted so set this to 1

  // web page
    const int gcodeTextHeight = 15;                      // Size of text box on main web page for entering gcode
    const int gcodeTextWidth = 50;

  const int p1HoldButtonDelay = 5000;                    // how long to wait when HOLD button is pressed on page 1 (ms)

  #define WDT_TIMEOUT 60                                 // timeout of watchdog timer (seconds) - i.e. auto restart if sketch stops responding

  const char* HomeLink = "/";                            // Where home button on web pages links to (usually "/")
  const uint16_t ServerPort = 80;                        // ip port to serve web pages on (usually 80)

  int dataRefresh = 2;                                   // Refresh rate of the updating data on root web page (seconds)

  const byte LogNumber = 75;                             // number of entries in the system log

  unsigned long wifiRetryTime = 30;                      // how often to try to reconnect to wifi if connection is lost (seconds)   

  const byte noOfCoordinates = 4;                        // number of coordinate systems available
  int currentCoord = 0;                                  // active coordinate    (0 to noOfCoordinates - 1)
  
  const int maxGcodeStringLines = 512;                   // maximum number of lines of gcode allowed
  const int estimateAverageLineLength = 30;              // average line length

  // CYD - Display 
    #define SCREEN_ROTATION 1
    #define SCREEN_WIDTH 320
    #define SCREEN_HEIGHT 240
    #define SCREEN_BACKLIGHT 21


  // Digital calipers

    float highestAllowedReading = 9999.00;     // readings outside this range are flagged as an error
    float lowestAllowedReading  = -999.00;

    // structure for the calipers
      struct caliperStruct {
        const String title;                     // title of caliper (just a single upper case letter is best, e.g. X, Y and Z)
        const bool enabled;                     // if caliper is enabled
        const int clockPIN;                     // gpio pins
        const int dataPIN;
        bool direction;                         // set to 1 is direction is reversed
        unsigned long lastReadTime;             // last time a reading was received (millis)
        float reading;                          // current reading
        int error;                              // error status (0=ok)
        float adj[noOfCoordinates];             // adjustment of caliper reading to displayed reading for each coordinate system
      };

    // define calipers in use
      const int caliperCount = 3;               // number of calipers below
      
      caliperStruct calipers[] {  
        // Items: Axis name (single character, upper case), if enabled, clock gpio pin, data gpio pin, direction (1=reversed), 0, 0.0, 0, {0.0}
        // NOTE: Some of the menus and buttons expect there to be 3 axes but you can set the enabled to '0' if they are not required

        { "X", 1,  0,  4, 0, 0, 0.0, 0, {0.0} },        // Note: pin 0 is the onboard button (it can stop the device rebooting after programming)
        
        { "Y", 1, 17, 16, 0, 0, 0.0, 0, {0.0} },
        
        { "Z", 1, 22,  5, 0, 0, 0.0, 0, {0.0} }         // Note: pin 5 is used by the SD card (chip select)
        
      };

  // CYD - Touchscreen
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

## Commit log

2023-12-24 connector
    Takes the 10 wires from the esp32 module and breaks it out to the 3 digital calipers
    [FRITZING-connector.fzz]
2023-12-26 connector
    This is just a breakout board which takes the ribbon cable and converts it to 4 connectors for the DROs
    [FRITZING-connector.fzz]
2023-12-28 mod to try and give the circuit some extra protection
2024-01-02 casing for the digital calipers
    [caliperCasingv.FCStd]
2024-01-18 caliper attached to lathe
